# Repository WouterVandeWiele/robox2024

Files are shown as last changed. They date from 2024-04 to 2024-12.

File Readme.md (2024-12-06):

# Robox 2024 (Update is here!)



### status updates
- update 21/10/2024 ==> you can download the update here: https://woutervandewiele.github.io/robox2024/
- update 17/09/2024 ==> We had some issues while testing the update, but we are slowly ironing out most of these issues. The update will contain: possibility of adding radio stations
- update 27/08/2024 ==> We are working on the update.

### planned software updates
- adjusting motor speed in the settings menu (currently being tested)
- fixing full battery indication (currently being tested/in development))
- remembering last played radio station (in development)
- adding a sleep timer (maybe ==> in consideration)

### 1_1_0 update, shoutout to Wouter! (read the dutch part of the manual for the update procedure)
- adding radio stations (read the dutch manual about the part of adding radio stations)
- remembering what audio source was used last, the radio now remembers if you last time played a radio station or a bluetooth stream or ...

### planned mechanical updates
- 3D-printable or foldable glasses (in front of the speakers) ==> in development (30/10/2024)
- Replacing wheels with other fun gadgets (e.g. waving hands) ==> in development (30/10/2024)
- Added a longer version of the ear axle holder, so the wheels are separated a bit further from the body. (see 3D-print files)


- Added a full 3D-printed wheel (as one part)



English version below.

Welkom bij het Robox 2024 (v2) project. Hier vind je alle informatie omtrent dit project. Voor de aanloop van FRI3D hebben we al wat basisinformatie gepubliceerd om je wegwijs te maken met de radio. In de weken na het kamp gaan we nog wat updates toevoegen om de functionaliteit van Robox v2 te verbeteren en uit te breiden. Dus hou deze website in het oog. Er zal dan uitgelegd worden hoe je zelf de udpate kan uitvoeren. Om deze website terug te vinden volstaat het om de QR-code op de achterkant van de radio te scannen.

- status update: de eerste update is klaar en verkrijgbaar. We gaan ook de documentatie op deze site uitbreiden en trachten in het nederlands en engels aan te bieden.
- Voor degenen die het project nog verder willen steunen of een bijdrage willen leveren mogen een donatie doen via https://buymeacoffee.com/erowin
- Heb je vragen over het project kan je via github een issue openen of ons contacteren via discord in deze server: https://discord.gg/HG2vBjpU9c (vragen naar @erowin of @wally)

Welcome at the Robox 2024 (v2) project, here you will find all information about this project. Before FRI3D we have already published some basic information to get to know your radio. In the next comming weeks after the camp we will add some firmware updates to increase the functionality of Robox V2. So keep an eye on this site. There will appear an explanation on how to execute the update all by yourself. To find back this webpage you can scan the QR-code on the back of the radio.

- update: the first firmware update has been releas and can be downloaded here: https://woutervandewiele.github.io/robox2024/ (check the dutch manual for the installation of the update)
- For the ones who want to support the project can donate here: https://buymeacoffee.com/erowin
- If you have questions about the project you can contact us on discord in this server: https://discord.gg/HG2vBjpU9c (you can ask for @erowin or @wally)

## Handleiding

### Beschrijving



1)	Aan/Uit-schakelaar: kan je de luidspreker mee aan of uitzetten. Om te laden dient deze aan te staan.
2)	Menubediening (knop): dient om door de menu’s op het scherm te navigeren. (“bron selectie”, “afspelen”, “instellingen”)
3)	Muziekbediening (knop): dient om de muziek te kunnen bedienen.



Functies:
 
De luidspreker kan muziek afspelen via:

•	Bluetooth

•	Wifi (webradio) 

•	microSD-kaart (.mp3)

•	geen muziekbron

1.	Party modes:

•	Leds op het ritme van de muziek.

•	Wielen die bewegen op het ritme van de muziek.

•	Combinatie van beide.

2.	Batterij:

•	Bijna leeg ==> batterij icoon gaat aan

•	Leeg ==> batterij icoon knippert

•	Opladen wordt aangeduid door een knipperend “zonnetjes” symbool. Als de batterij volgeladen is, dan brandt het “zonnetjes” symbool gewoon.

3.	Menu-items (te bedienen met de menu-knop)
   


### Audiobronnen

Van audiobron wisselen doe je door naar het menu “Bron selectie” te gaan (symbool “dubbele gekruiste pijl). Volgende bronnen zijn beschikbaar:

•	Internetradio ==> Hierbij kan je kiezen tussen verschillende internetradiostations. 

  o	Als je “internetradio” kiest dan zal deze eerst proberen te verbinden met al gekende netwerken. Als deze niets vindt, of het lukt niet, dan zet deze zijn eigen wifi-netwerk op genaamd: “ROBOX-XXXXXXX”. (Zolang de “wifi” niet ingesteld is blijft deze op het scherm vasthangen). Je kan met je gsm/laptop verbinden met het wifi-netwerk van ROBOX, hier kan je dan het gewenste wifi-netwerk toevoegen waarmee ROBOX verbinding moet maken. Normaalgezien opent de webbrowser vervolgens automatisch een website (zie afbeelding rechts). Indien dit niet het geval is, dan kan je het volgende manueel in de adresbalk ingeven: http://192.168.4.1 Op deze website kan je dan het wifi-netwerk kiezen en vervolgens opslaan “save”. ROBOX zal proberen te verbinden met dit netwerk. Als dit niet lukt, dan zet deze terug zijn eigen wifi aan zodat je het opnieuw kan ingeven.



  o	Je kan zelf radiostations toevoegen door naar “Geen bron” te gaan en dan bij “Instellingen” kan je “Webconfiguratie” kiezen. Dan moet je terug surfen met je laptop naar ip adres dat bij in de instellingen staat. Bijvoorbeeld: http://192.168.1.183 in de adresbalk van je webbrowser ingeven.

  

  o	Je krijgt dan deze webpagina te zien waar je een webradiostream kan toevoegen.
  
  

  o	De stream die je toevoegd moet http:// zijn (https:// werkt niet). De link mag ook geen redirect zijn. Je kan dit testen in een webbrowser. Als de link een redirect uitvoert moet je de link hebben na de redirect. Het moet een mp3 stream zijn. Hier kan je de meeste radiostreams (België en wereldwijd) terugvinden: https://fmstream.org/index.php?c=FT

•	Bluetooth ==> Hierbij kan je bluetooth verbinding maken met een gsm/laptop en muziek afspelen. De bluetooth naam vindt je in de “Instellingen”.

•	microSD-kaart (mp3-speler) ==> Hierbij kan je muziek afspelen van een microSD-kaart.

•	Geen bron ==> Dan speelt ROBOX geen muziek af, maar kan je extra instellingen doen via “Instellingen” en “Webconfiguratie” door vervolgens te surfen naar het ip-adres dat ook in “Instellingen” staat. (zie afbeelding rechts)

### Firmware update installeren
- Sluit de radio met een USB-data kabel aan op de pc.
- Ga naar https://woutervandewiele.github.io/robox2024/ en selecteer de meest recente versie, bijvoorbeeld fried_1_1_0.

- Klik vervolgens op install
- Selecteer de juiste com-poort (zie apparaatbeheer ==> poorten om te weten welk apparaat de radio is) en klik op connect.

- Het kan enkele minuten duren vooraleer de update uitgevoerd is.

- Neem contact met ons op als het updaten niet lukt.

## Configuration

main.cpp is configurable through defines to select different examples or components.

### Audio components

Configuration of the arduino audio library components. 
In the context of the robox project they all drive the I2S amp and thus only one can be enabled at a time.

Select one of:

```h
#define ROBOX_FULL          //  the complete audio project, with audio mux

// the examples, from the arduino audio library, with minimal adaptations
#define ROBOX_EXAMPLE_BLE
#define ROBOX_EXAMPLE_SD
#define ROBOX_EXAMPLE_WEB

// robox components, based on the examples above, with adaptations for the audio mux
#define ROBOX_COMPONENT_BLE
#define ROBOX_COMPONENT_WEB
#define ROBOX_COMPONENT_SD
```

### addon components

Additional functionality can be included or removed, multiple can be selected:
```h
#define ROBOX_LCD         // include the LCD component (headers, init and loop)
#define ROBOX_DEBUG_CLI   // include the debug CLI component (headers, init and loop)
```

### wifi credentials

In order to use the webstream component, wifi credentials need to be added to access the web. Follow the instructions here: [wifi credentials](lib/WIFI_CREDENTIALS/README.md)

## Debug CLI

To ease manual testing a debug CLI is added (configurable through the preprocessor statements)
Open a serial connection and when the the ESP starts, follozing messages are displayed if the CLI is initialized.

```
>>> Starting debug CLI.
>Ping was added to the CLI!
>Help was added to the CLI!
>Print was added to the CLI!
>Source was added to the CLI!
>>> CLI installed, type "help" for all options.
```

Currently following options are implemented:
```
help
# help
ping
Replies with "pong" if the ESP32 is still going through the main loop

help
Print cli help, lists all registered commands

print -text <value> [-n <1>]
Example command demonstrating aruments, takes <text> and prints n times

source -s <value>
Select the audio source, takes 1 arument of: ['ble', 'web', 'sd']

mux -meta_title -volume <value>
(get/set mux settings)
-meta_title: reads the current title of the song
-volume: sets the colume on the stream
```

## patching URLStream
In order to check the user URL stream and display an error if the URL is invalid,
a pach is needed on the aurduino audio tools library:

```shell
cp .\URLStream.patch .pio\libdeps\robox_hw\audio-tools
cd .pio\libdeps\robox_hw\audio-tools
cat .\URLStream.patch | git apply
```

## PlatformIO configuration (dev log)
### Freenove fnk0085
https://community.platformio.org/t/esp32s-configuration-error/38647/2

Copy the freenove_fnk0085.json to the projects boards folder.

`.platformio\platforms\espressif32\boards`

## JTAG debugger (ESP32-WROOM-DA)

https://www.youtube.com/watch?v=ENLhW0MQuu0

----

https://www.reddit.com/r/esp32/comments/pvidlt/rst0x10_rtcwdt_rtc_resetboot0x33_spi_fast_flash/

It's always good to read the datasheet. GPIO12 (aka MTDI) is a strapping pin, and when pulled low at boot sets the internal voltage regulator (VDD_SDIO) to 1.8 V. Most dev boards use 3.3 V flash, so... 

----

https://www.reddit.com/r/esp32/comments/yw1w0a/cant_tell_what_name_will_this_show_with_in/

It will work because it's based on the ESP32 generic. The problem is that the DA module has the RF switch connected to 2 different GPIOs that the Wi-Fi API controls.

Be sure you are not using GPIO2 and GPIO25 when using the DA module.

## ESP32 partition calculator
https://esp32.jgarrettcorbin.com/
https://atctwo.net/projects/esp32-partition-editor/

## burn set_flash_voltage

```shell
pip install cryptography
pip install ecdsa
pip install bitstring
pip install reedsolo
```

PlatformIO Core CLI:
```shell
pio pkg exec -- espefuse.py set_flash_voltage 3.3V --port COM3
```

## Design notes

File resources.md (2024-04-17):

# ESP32 DevkitM-1

Devkit speciffic: https://docs.espressif.com/projects/esp-idf/en/stable/esp32/hw-reference/esp32/user-guide-devkitm-1.html

## ESP32 SPI

API & pins: https://docs.espressif.com/projects/esp-idf/en/release-v3.0/api-reference/peripherals/spi_master.html

FAQ HSPI vs VSPI: https://docs.espressif.com/projects/esp-faq/en/latest/software-framework/peripherals/spi.html

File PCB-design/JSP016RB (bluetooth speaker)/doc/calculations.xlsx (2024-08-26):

Motor controller |  |  |  |  |  | Motor selection |  |  | Locked current
Vsense > Vref ==> output power disabled |  |  |  |  |  | 12GAN20-30 | 150RPM | 3V | 0.23 | A
Vref | 0.4114058355 | V | 0,1V < Vref < 0,5V |  |  |  |  |  | correct?
Rtop | 330000 | Ohm
Rbot | 47000 | Ohm
VCC | 3.3 | V
Rsense | 0.8228116711 | Ohm
Vsense | 0.4114058355 | V | (trip point)
Iloadpk | 0.5 | A
Prsense | 0.2057029178 | W
Iloadpk | 0.5142572944 | A
Vsense | 0.4114058355 | V
Rsense | 0.8 | Ohm
Prsense | 0.2115684519 | W
Boost converter
Vin | 3.6 | V | Dnom | 0.371 |  | Dworst | 0.595 |  | Dbest | 0.244
Dnom | 0.371 |  | Vin | 3.7 | V | Vin | 2.7 | V | Vin | 4.2 | V
f | 3800000 | Hz | n | 0.85 |  | n | 0.75 |  | n | 0.9
L | 1e-06 | H | Vout | 5 | V | Vout | 5 | V | Vout | 5 | V
Iout | 1.5 | A
Ilpk | 2.560474521 | A |  | Output cap
 |  |  |  | Cmin | 9.078947368e-06 | F
Worst case |  |  |  | Iout | 1.5 | A
Vin | 3.6 | V |  | Vout | 5 | V
Dworst | 0.595 |  |  | Vin | 2.7 | V
f | 3800000 | Hz |  | f | 3800000 | Hz
L | 1e-06 | H |  | DV | 0.02 | V
Iout | 1.5 | A | ==> may not go higher then this
Ilpk (worst) | 3.985545809 | A

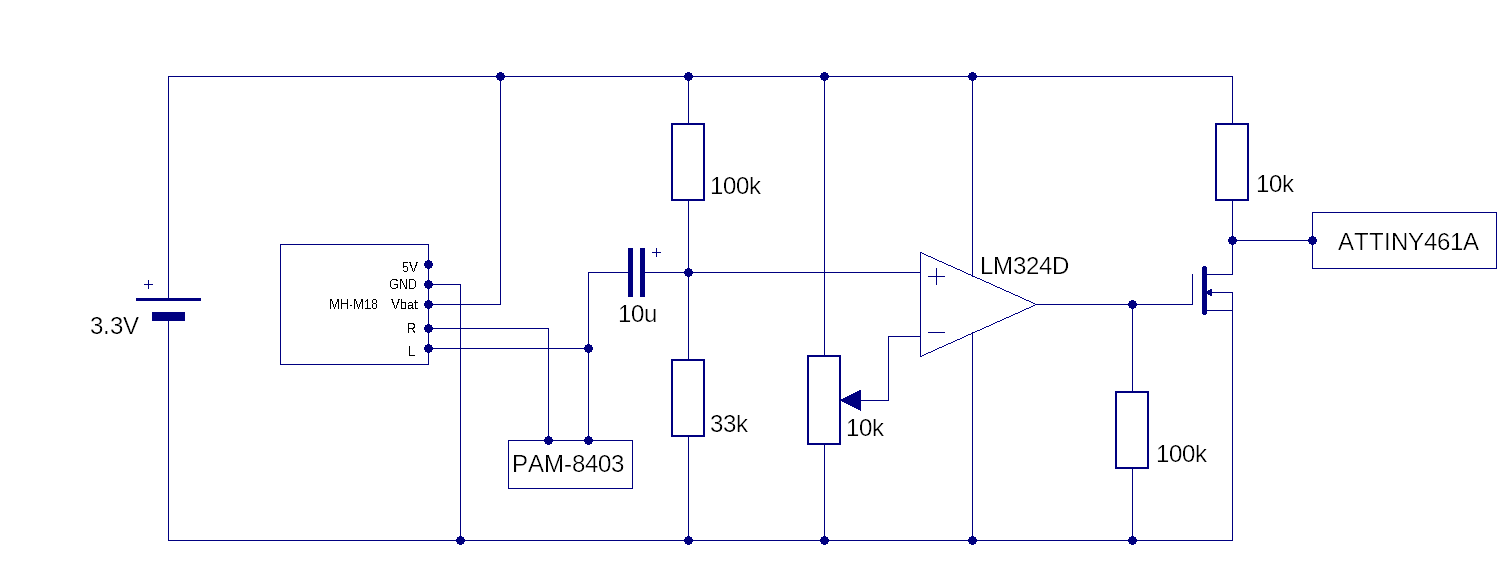
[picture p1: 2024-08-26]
PCB-design/JSP016RB (bluetooth speaker)/robox.BMP

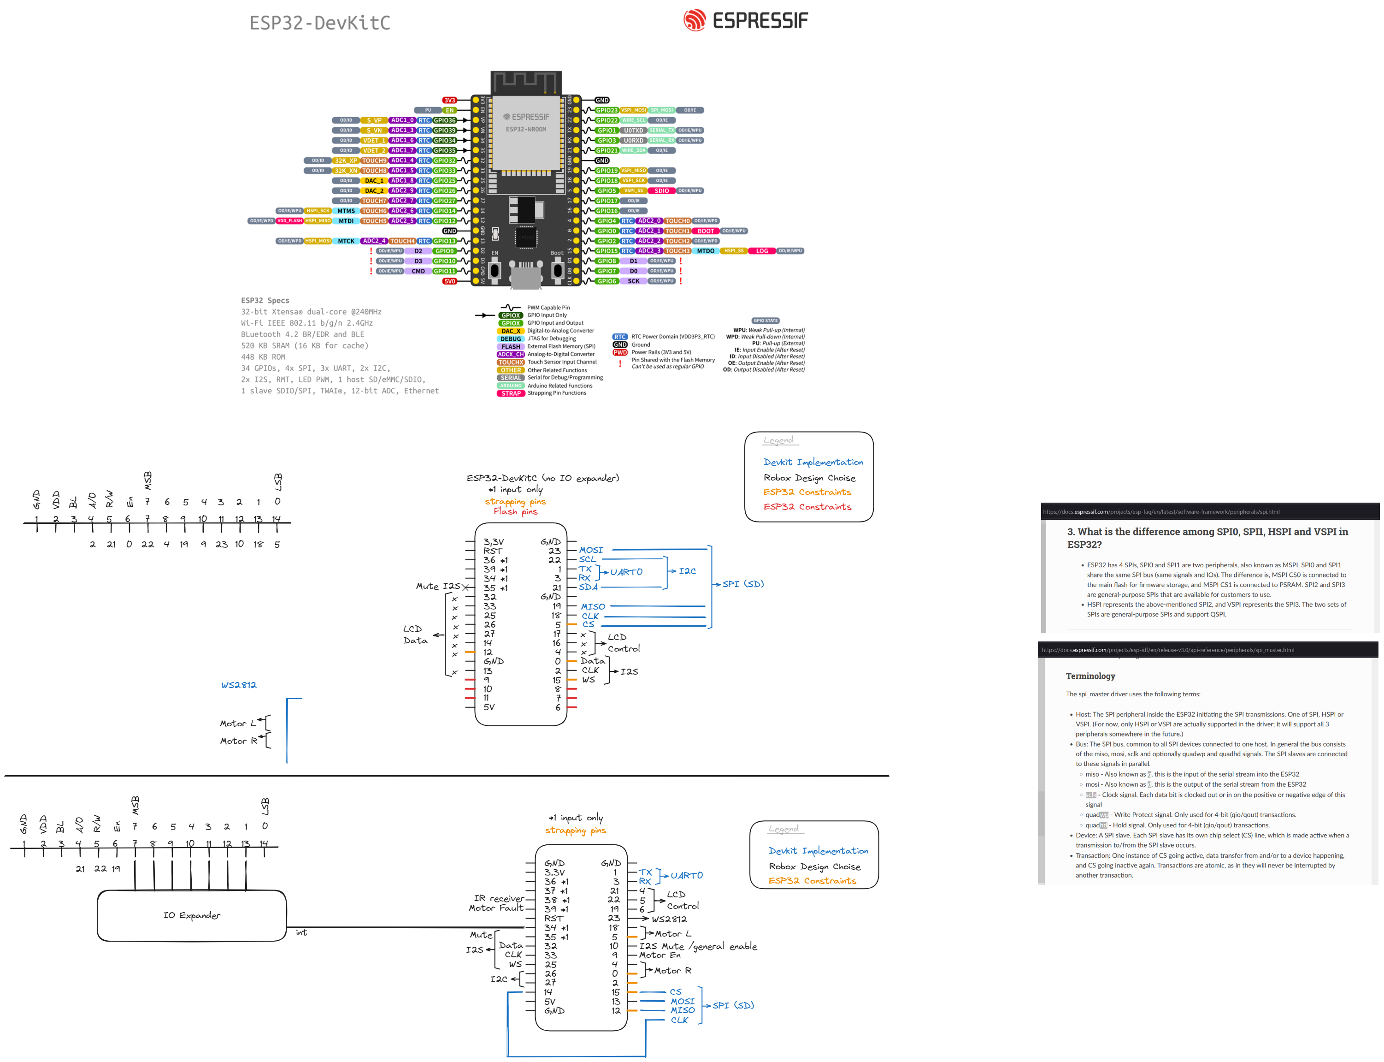
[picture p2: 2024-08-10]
docs/static/pinout_devkitC.excalidraw.png

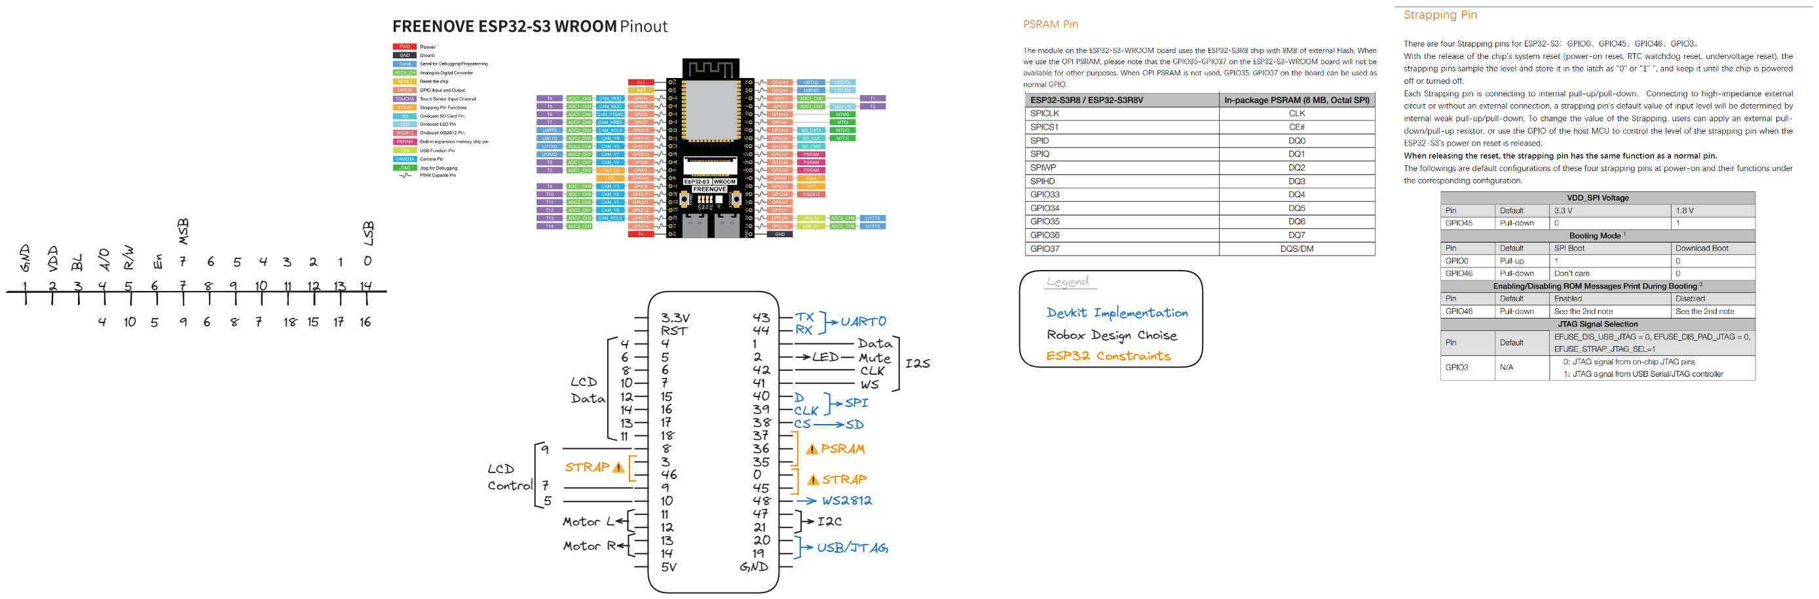
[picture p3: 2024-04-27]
docs/static/pinout_freenove.excalidraw.png

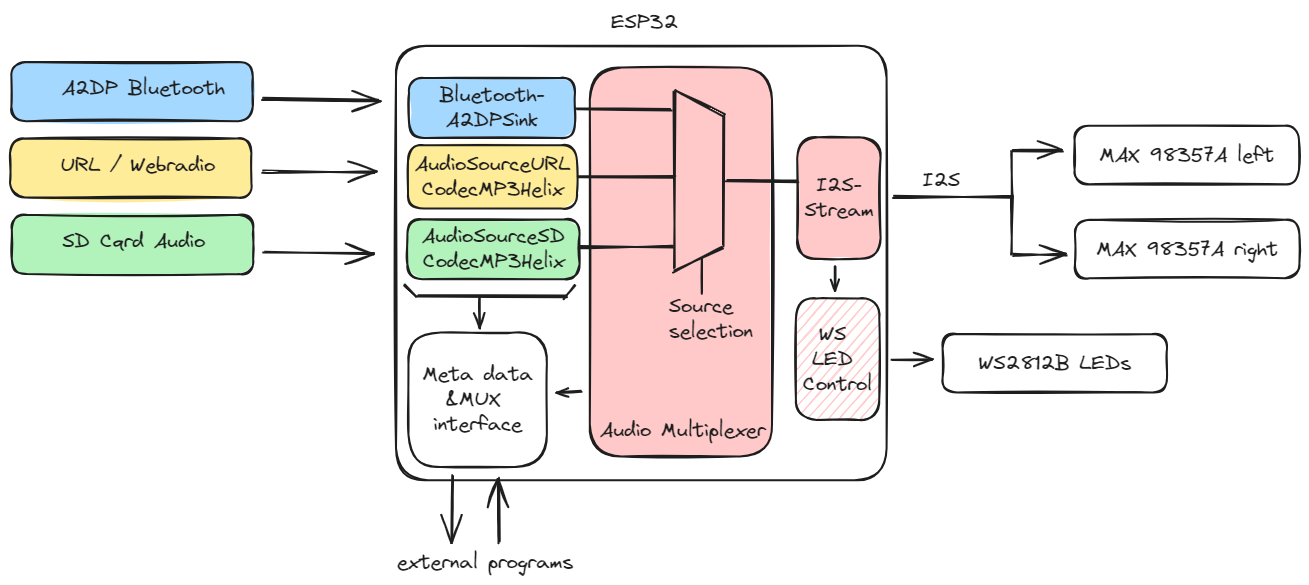
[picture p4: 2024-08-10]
docs/static/audio_overview.excalidraw.png

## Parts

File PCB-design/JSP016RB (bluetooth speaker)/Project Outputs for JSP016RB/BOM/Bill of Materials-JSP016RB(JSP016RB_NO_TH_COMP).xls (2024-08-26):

manufacturer | Description | Designator | LibRef | Quantity | supplier_1 | supplier_1_partnumber
Stackpole Electronics Inc | RES 2.2K OHM 5% 1/16W 0402 | R18 | 52 | 1 | digikey | RMCF0402JT2K20CT-ND
Stackpole Electronics Inc | RES 5.1K OHM 1% 1/16W 0402 | R2, R3 | 94 | 2 | digikey | RMCF0402FT5K10CT-ND
Diodes Incorporated | IC XPNDR 400KHZ I2C 24TSSOP | IC10 | 83 | 1 | digikey | PI4IOE5V6416LEXDICT-ND
Panasonic Electronic Components | RES SMD 330 OHM 1% 1/10W 0402 | R17 | 21 | 1 | digikey | P330LCT-ND
Panasonic Electronic Components | RES SMD 100K OHM 1% 1/10W 0402 | R14, R21, R22, R23, R25, R26, R27, R29, R34, R35, R38, R40, R41, R63, R67, R74, R75 | 7 | 17 | digikey | P100KLCT-ND
Panasonic Electronic Components | RES SMD 10K OHM 1% 1/10W 0402 | R4, R19, R55, R56, R61 | 6 | 5 | digikey | P10.0KLCT-ND
Panasonic Electronic Components | RES SMD 4.7K OHM 1% 1/10W 0402 | R32, R33, R45, R46, R66 | 1 | 5 | digikey | P4.70KLCT-ND
Panasonic Electronic Components | RES SMD 1K OHM 1% 1/10W 0402 | R15, R51 | 0 | 2 | digikey | P1.00KLCT-ND
Panasonic Electronic Components | RES SMD 0 OHM JUMPER 1/10W 0402 | R5, R8, R31, R37, R39, R57, R58, R59, R60, R62, R64, R69, R70, R72, R73 | 8 | 15 | digikey | P0.0JCT-ND
Diodes Incorporated | MOSFET N-CH 100V 170MA SOT23-3 | Q1, Q2, Q5 | 7 | 3 | digikey | NTR4003NT1GOSCT-ND
Maxim Integrated | IC AMP CLASS D MONO 3.2W 16TQFN | IC1, IC2 | 91 | 2 | digikey | MAX98357AETE+TCT-ND
onsemi | MOSFET 2N-CH 6CSP | Q3 | 18 | 1 | digikey | EFC8811R-TFOSCT-ND
Diodes Incorporated | MOSFET P-CH 20V 820MA SOT323 | Q4 | 14 | 1 | digikey | DMG1013UW-7DICT-ND
Stackpole Electronics Inc | RES 0.003 OHM 1% 1.5W 2010 | R20 | 28 | 1 | digikey | CSNL2010FT3L00CT-ND
WCH(Jiangsu Qin Heng) | 2Mbps Transceiver USB 2.0 SOP-16 USB ICs ROHS | IC4 | 79 | 1 | lcsc | C84681
TOPPOWER | IC ESOP-8 Battery Charger Management | IC8 | 89 | 1 | lcsc | C16581
TE Connectivity Passive Product | CRGCQ 0402 27R 1% | R16 | 55 | 1 | digikey | A129608CT-ND
Thin Film Technology Corp. | RES 0.002 OHM 1% 1W 1206 | R52, R53 | 92 | 2 | digikey | 4463-D1MPC1206DR002FF-T5TR-ND
CIT Relay and Switch | SWITCH TOGGLE SPDT 5A 120V | S3 | 3 | 1 | digikey | 2449-ANT11SF1CQE-ND
CUI Devices | MICRO SD CARD CONNECTOR, 8 POSIT | J7 | 56 | 1 | digikey | 2223-MSD-11-ACT-ND
Espressif Systems | RF TXRX MOD BT TRACE ANT CHAS MT | IC3 | 80 | 1 | digikey | 1965-ESP32-MINI-1-N4CT-ND
Nexperia USA Inc. | IC GATE AND 1CH 2-INP 5TSSOP | IC11 | 95 | 1 | digikey | 1727-6053-1-ND
Adafruit Industries LLC | ADDRESS LED DISCRETE RGB 4X2MM | D1, D2 | 86 | 2 | digikey/mouser | 1528-4691-ND/485-4691
Samsung Electro-Mechanics | CAP CER 4.7UF 25V X5R 0805 | C14, C21, C22 | 44 | 3 | digikey | 1276-1244-1-ND
Samsung Electro-Mechanics | CAP CER 1UF 16V X5R 0402 | C16, C18 | 5 | 2 | digikey | 1276-1067-1-ND
Samsung Electro-Mechanics | CAP CER 10000PF 50V X7R 0402 | C48, C49 | 7 | 2 | digikey | 1276-1028-1-ND
Amphenol ICC (Commercial Products) | USB2.0, TYPE C, MID MOUNT, CENTE | J2 | 55 | 1 | digikey | 664-GSB1C4621DS1HRCT-ND
Pulse Electronics | FIXED IND 1UH 5.8A 26 MOHM SMD | L5 | 14 | 1 | digikey | 553-3287-1-ND
Vishay Dale | RES SMD 100 OHM 1% 1/5W 0402 | R6, R28, R43, R44, R47, R48, R65 | 29 | 7 | digikey | 541-100YCT-ND
STMicroelectronics | IC HALF BRIDGE DRV 1.3A 16VFQFPN | IC13 | 81 | 1 | digikey | 497-16604-1-ND
Murata Electronics | CAP CER 10UF 25V X5R 10% SMD | C2, C6, C10, C19, C20, C31, C46 | 1 | 7 | digikey | 490-18214-1-ND
Murata Electronics | CAP CER 0.1UF 50V X5R 0402 | C3, C7, C11, C15, C17, C32, C34, C36, C37, C38, C47 | 0 | 11 | digikey | 490-16356-1-ND
Murata Electronics | THERMISTOR NTC 10KOHM 3380K 0402 | R13 | 1 | 1 | digikey | 490-4801-1-ND
Murata Electronics | CAP CER 0.022UF 50V X7R 0402 | C50 | 53 | 1 | digikey | 490-3884-1-ND
TE Connectivity | SWITCH NAVIGATION DGTL 50MA 12V | S1, S2 | 2 | 2 | digikey | 450-2425755-1CT-ND
TDK Corporation | FERRITE BEAD 120 OHM 0603 1LN | L1, L2, L3, L4 | 4 | 4 | digikey | 445-MMZ1608B121CTAH0CT-ND
YAGEO | CAP CER 1UF 25V X5R 0603 | C12 | 34 | 1 | digikey | 311-1445-1-ND
YAGEO | RES 210K OHM 1% 1/16W 0402 | R1 | 93 | 1 | digikey | 311-210KLRCT-ND
Texas Instruments | 3.8-MHZ, 5.25-V / 4-A BOOST CONV | IC5 | 84 | 1 | digikey | 296-48314-1-ND
Texas Instruments | IC BATT MON LI-ION 1CELL 8X2QFN | IC9 | 94 | 1 | digikey | 296-BQ298012RUGRCT-ND
Diodes Incorporated | IC REG LINEAR 3.3V 600MA SOT89-5 | IC6 | 85 | 1 | digikey | 31-AP2112R5-3.3TRG1CT-ND
YAGEO | RES 330K OHM 1% 1/16W 0402 | R49 | 65 | 1 | digikey | 13-RC0402FR-13330KLCT-ND
Yageo | RES SMD 5K OHM 1% 1/16W 0402 | R10 | 53 | 1 | digikey | 13-RC0402FR-075KLCT-ND
Yageo | RES SMD 46.4K OHM 1% 1/16W 0402 | R7, R24, R30, R36, R42, R50, R54 | 39 | 7 | digikey | 13-AC0402FR-0746K4LCT-ND

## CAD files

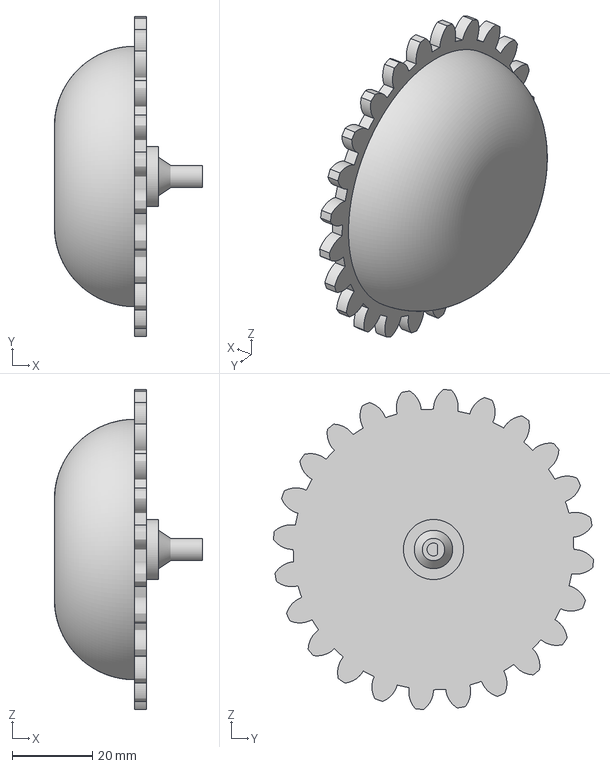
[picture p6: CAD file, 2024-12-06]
Mechanical design/3D-prints/fully-printed-wheel.3mf
37.0 x 79.8 x 79.8 mm

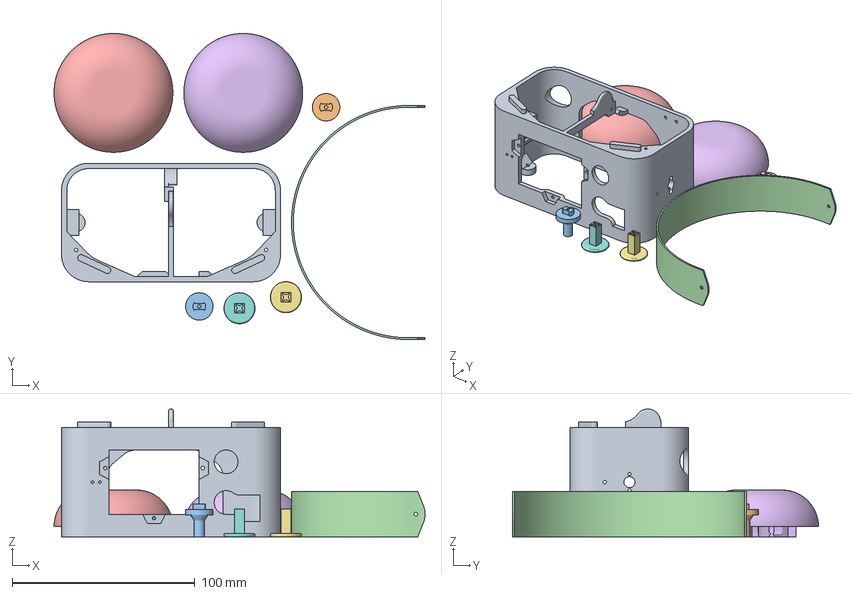
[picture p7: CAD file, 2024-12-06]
Mechanical design/3D-prints/1-full-set.3mf
202.9 x 167.4 x 70.0 mm
frame
ear axle
Headband
ear cap 3
button cap x 2

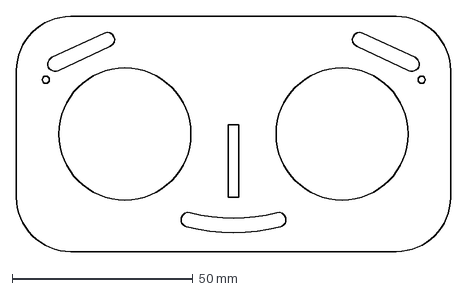
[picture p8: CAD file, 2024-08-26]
Mechanical design/Lasercutting/front plate/front-panel-20240725.dxf
120.0 x 65.0 mm

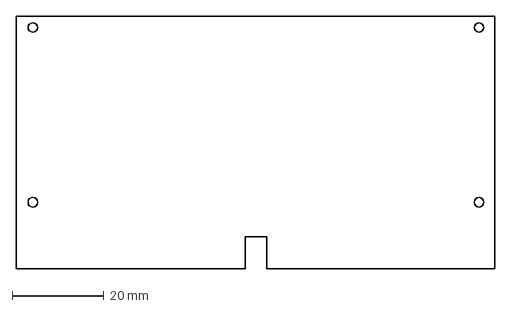
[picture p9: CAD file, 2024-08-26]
PCB-design/JSP016RB (bluetooth speaker)/doc/board-sketch.dxf
104.0 x 55.0 mm

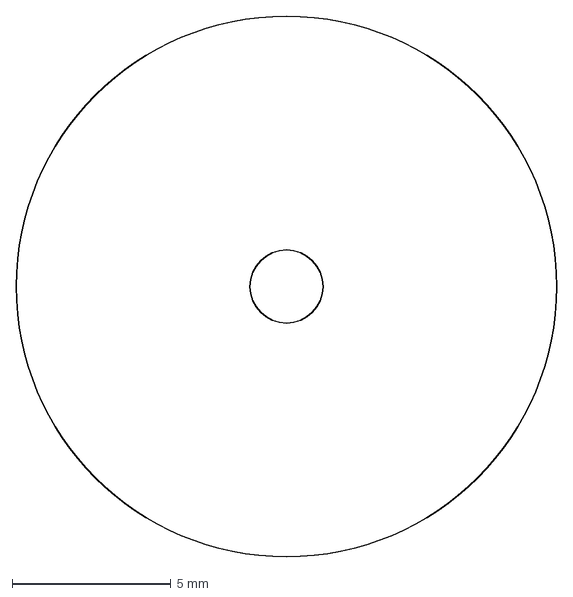
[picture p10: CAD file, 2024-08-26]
Mechanical design/Lasercutting/wheel/ear (gear cap).dxf
17.0 x 17.0 mm

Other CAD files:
Mechanical design/Lasercutting/rear plate/rear panel.dxf
Mechanical design/Lasercutting/sides/side.dxf
Mechanical design/Lasercutting/wheel/wheels.dxf

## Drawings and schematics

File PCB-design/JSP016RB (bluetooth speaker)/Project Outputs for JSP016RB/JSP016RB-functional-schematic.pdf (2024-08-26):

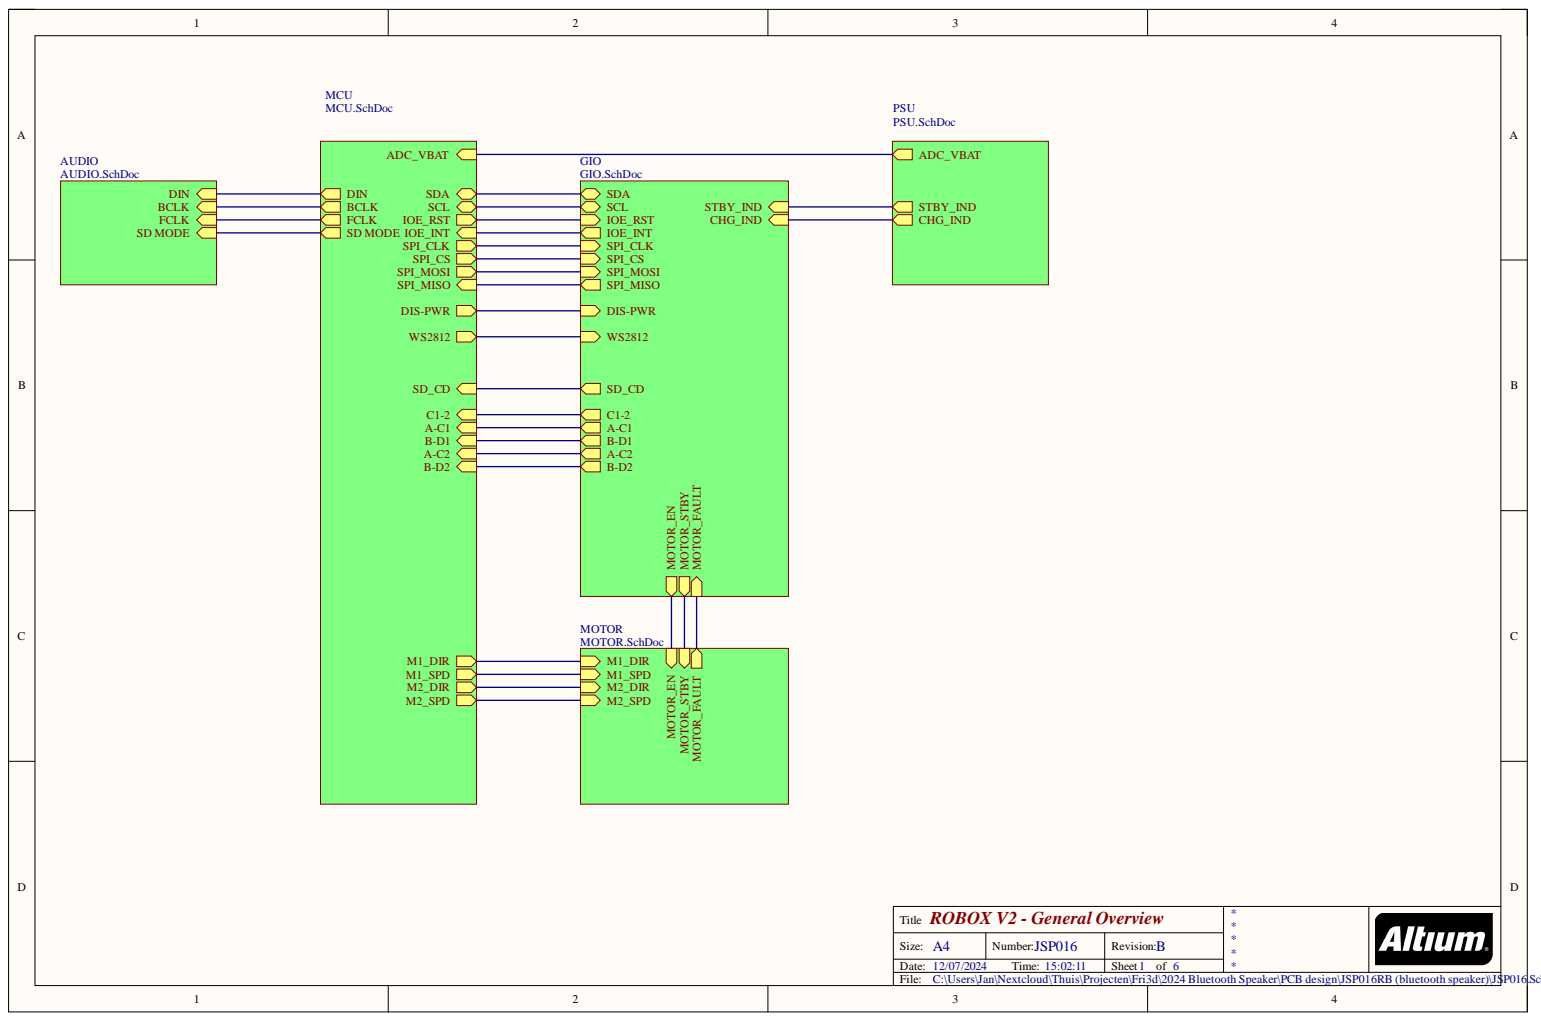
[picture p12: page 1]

C:\Users\Jan\Nextcloud\Thuis\Projecten\Fri3d\2024 Bluetooth Speaker\PCB design\JSP016RB (bluetooth speaker)\JSP016.SchDoc

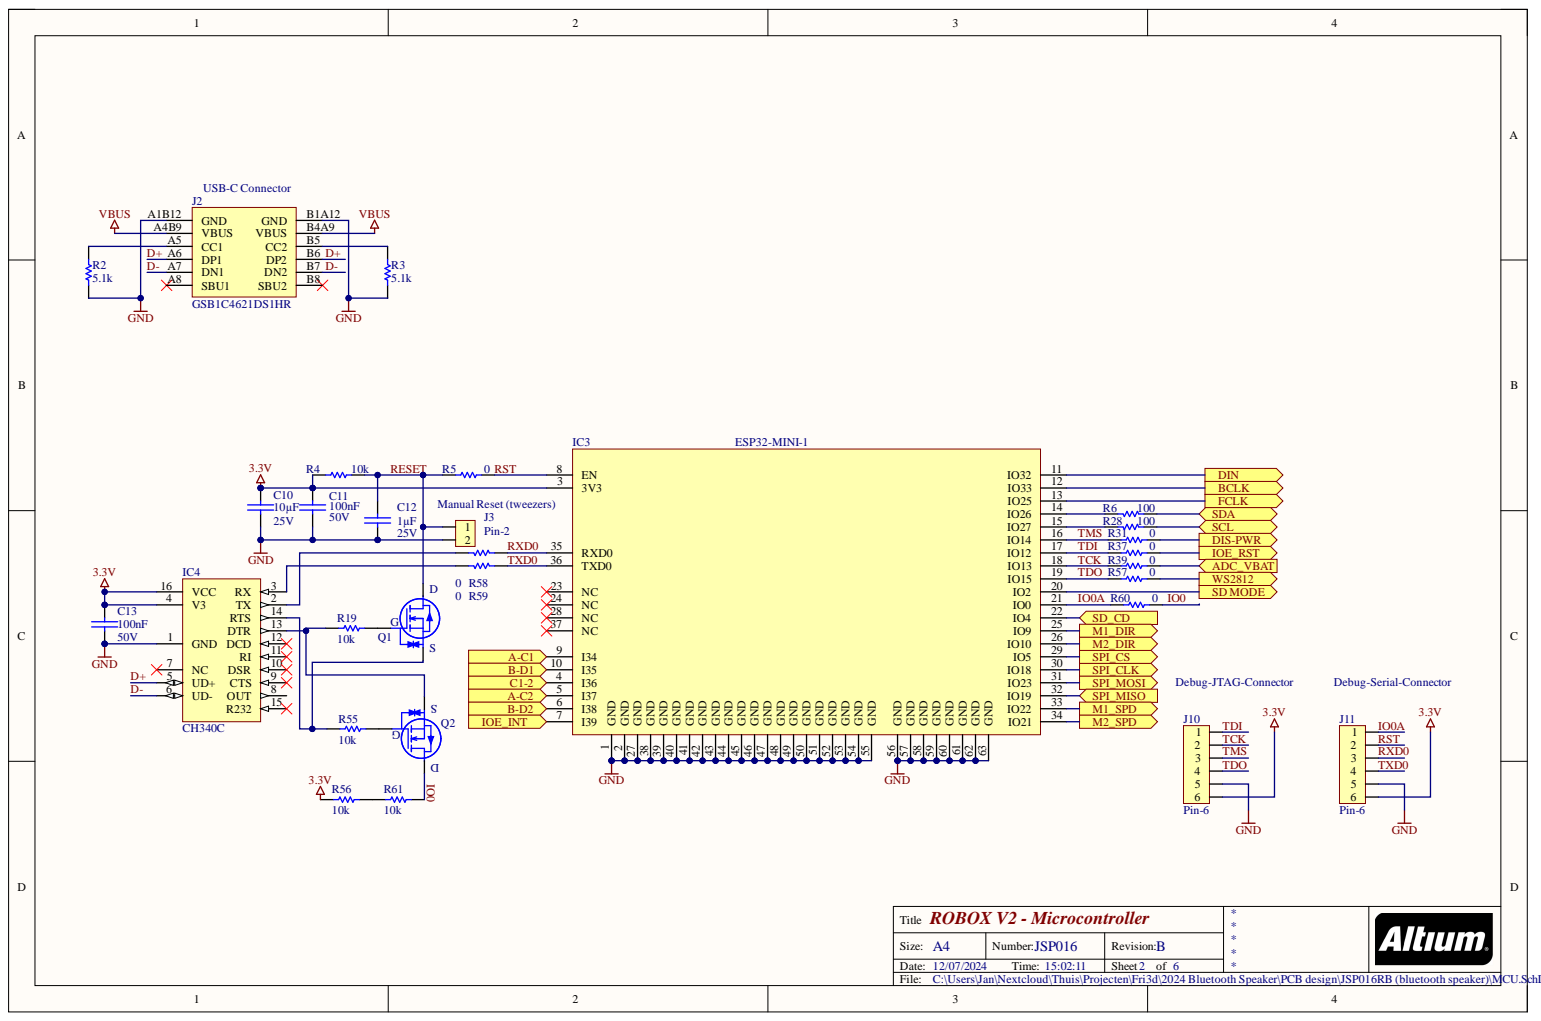
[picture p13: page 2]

C:\Users\Jan\Nextcloud\Thuis\Projecten\Fri3d\2024 Bluetooth Speaker\PCB design\JSP016RB (bluetooth speaker)\MCU.SchDoc

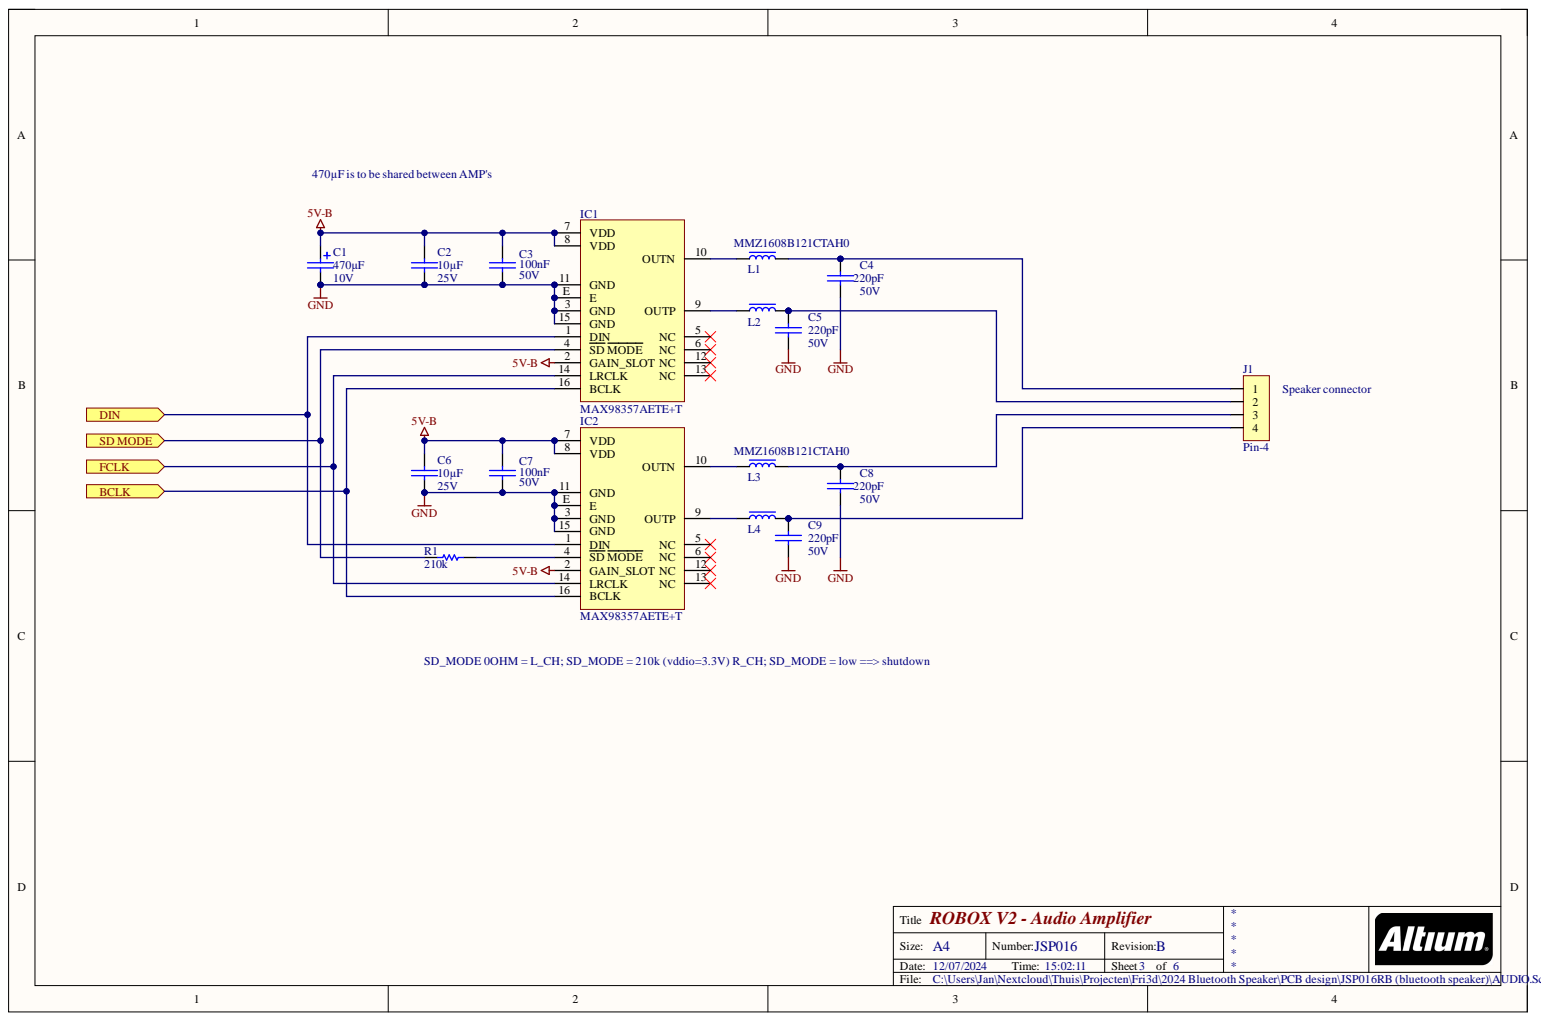
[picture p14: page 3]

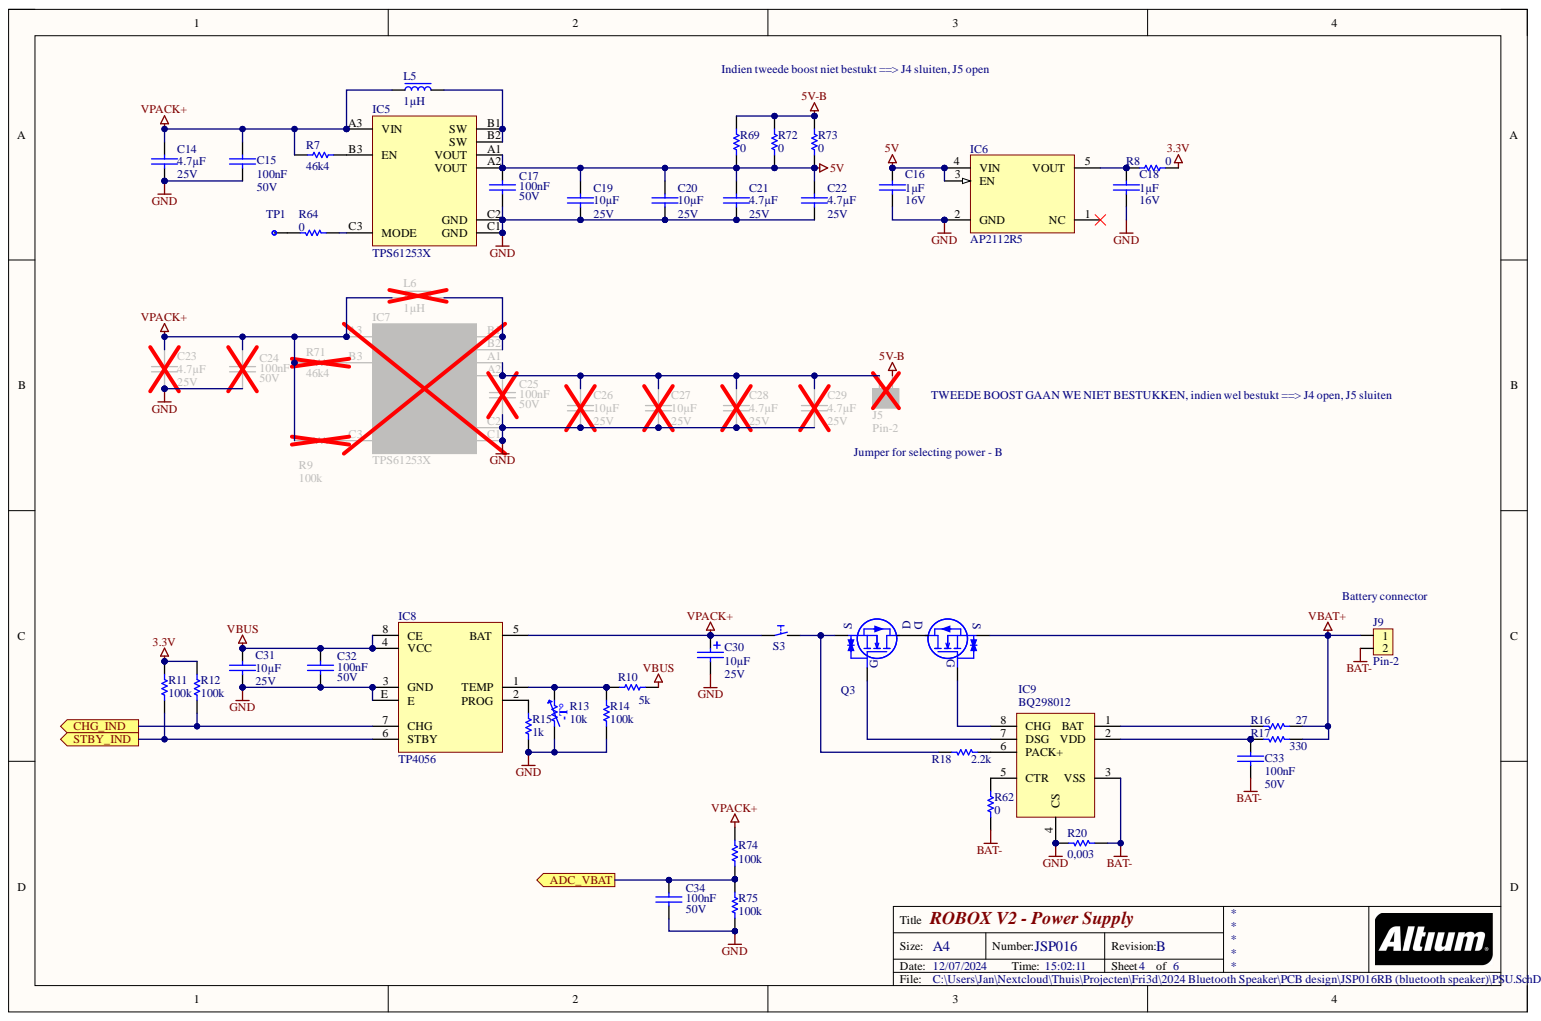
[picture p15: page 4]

Indien tweede boost niet bestukt ==> J4 sluiten, J5 open

TWEEDE BOOST GAAN WE NIET BESTUKKEN, indien wel bestukt ==> J4 open, J5 sluiten

Jumper for selecting power - B

C:\Users\Jan\Nextcloud\Thuis\Projecten\Fri3d\2024 Bluetooth Speaker\PCB design\JSP016RB (bluetooth speaker)\PSU.SchDoc

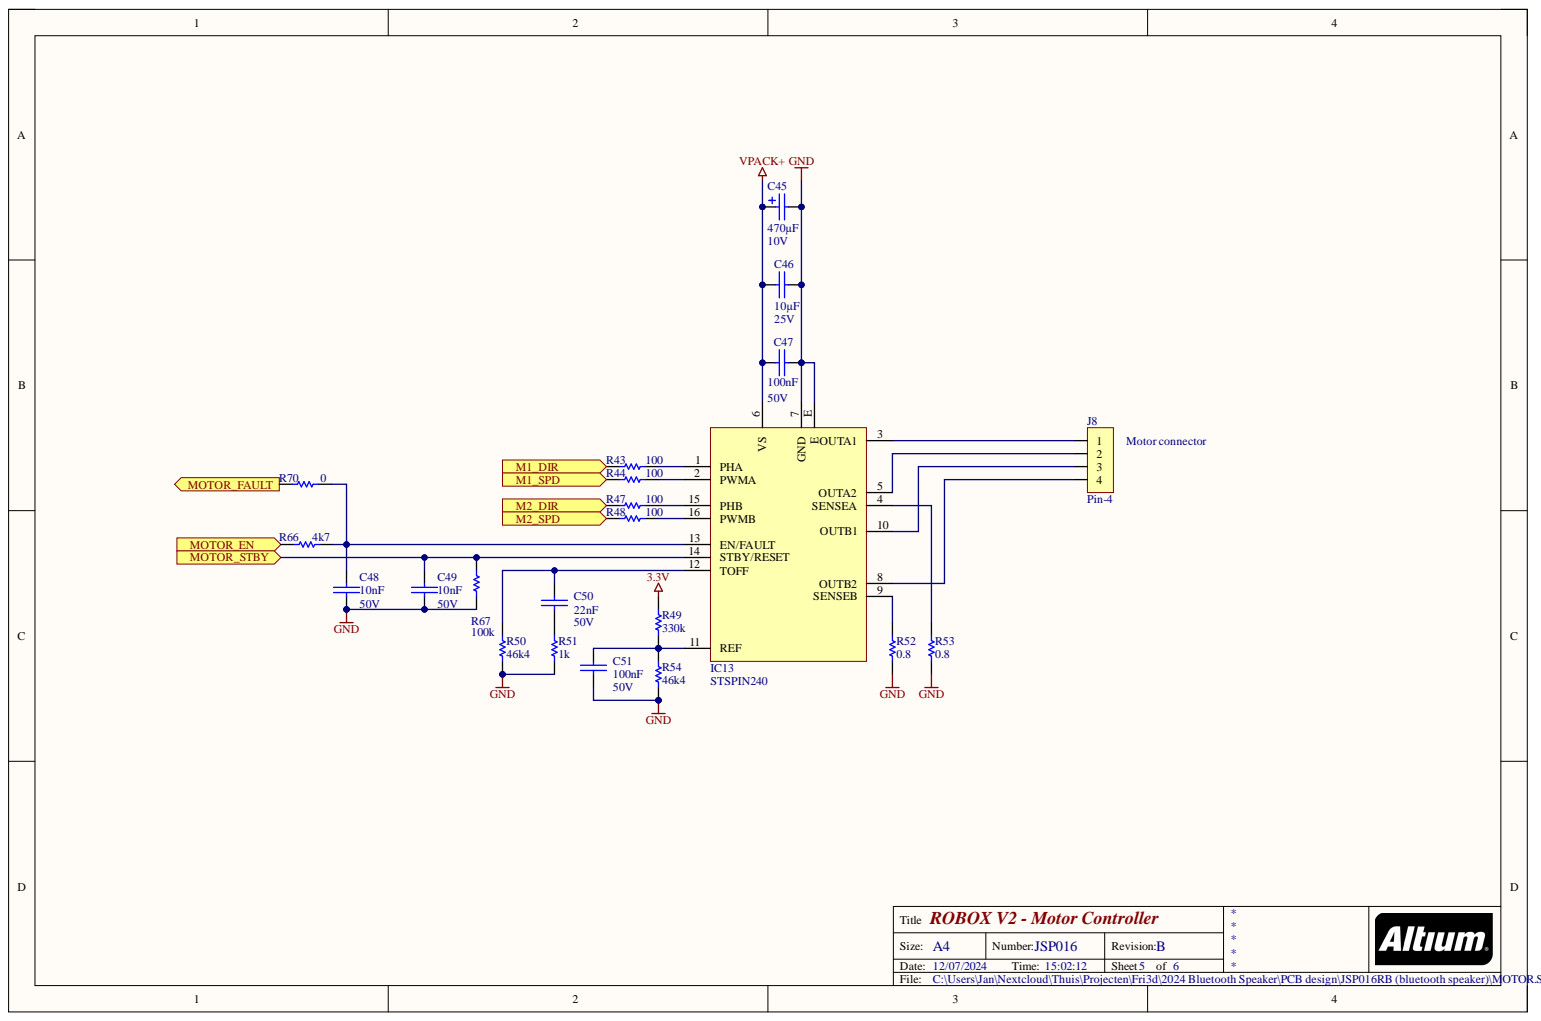
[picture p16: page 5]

C:\Users\Jan\Nextcloud\Thuis\Projecten\Fri3d\2024 Bluetooth Speaker\PCB design\JSP016RB (bluetooth speaker)\MOTOR.SchDoc

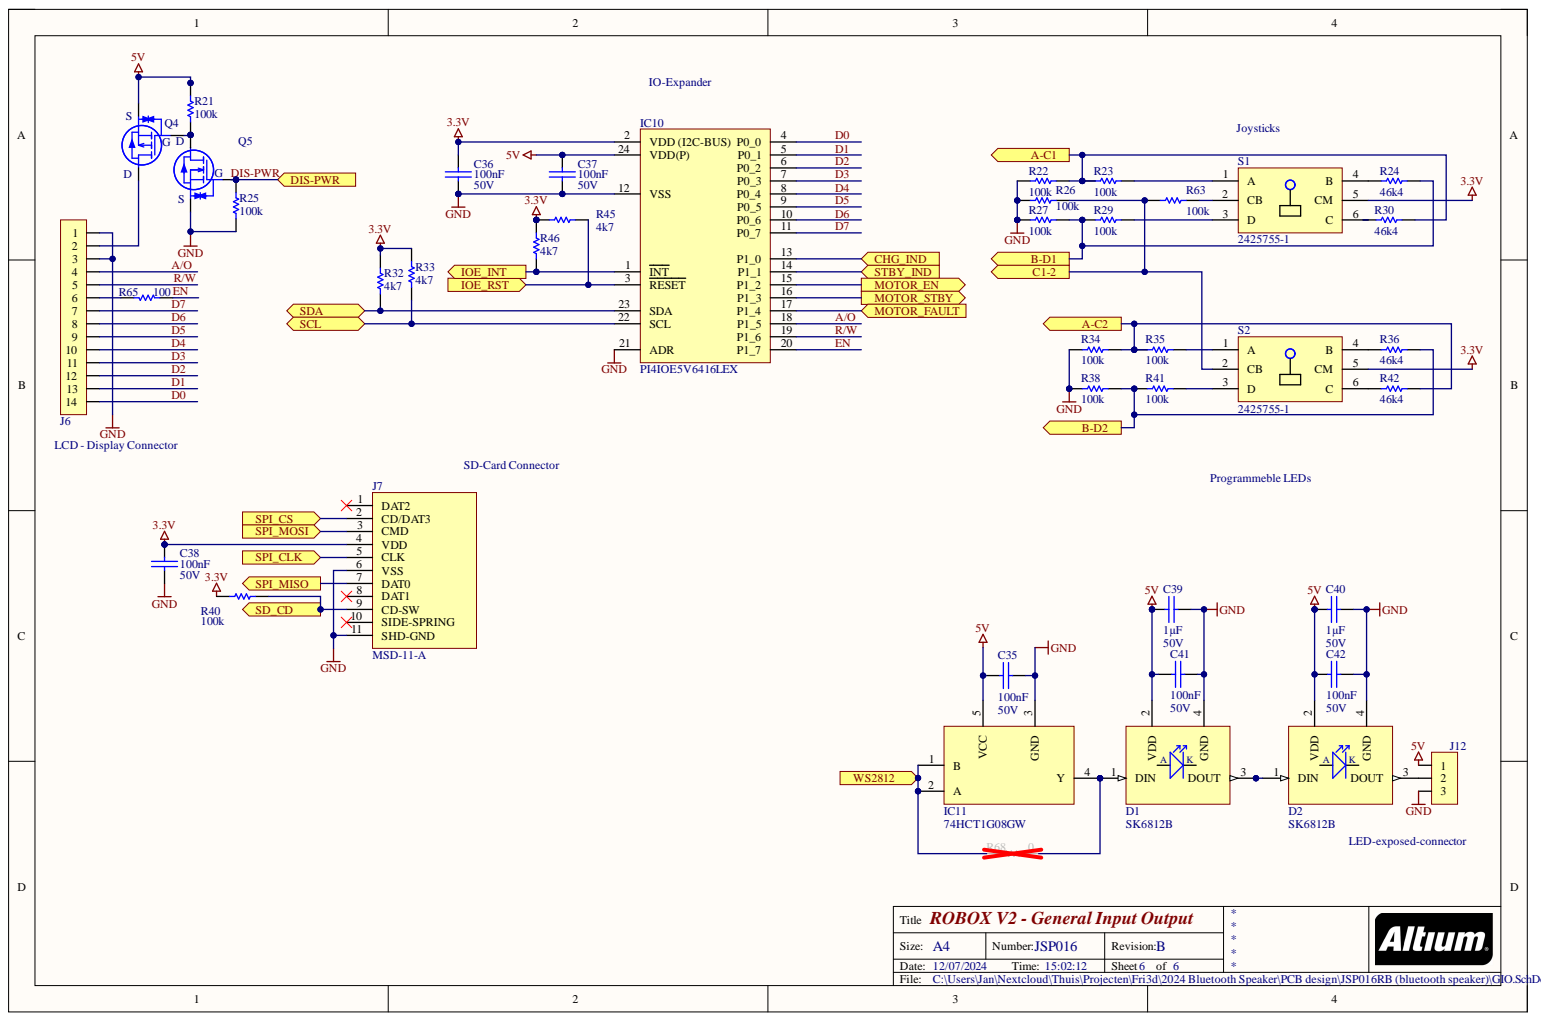
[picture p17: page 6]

DIS-PWR

ROBOX V2 - General Input Output
Title

C:\Users\Jan\Nextcloud\Thuis\Projecten\Fri3d\2024 Bluetooth Speaker\PCB design\JSP016RB (bluetooth speaker)\GIO.SchDoc

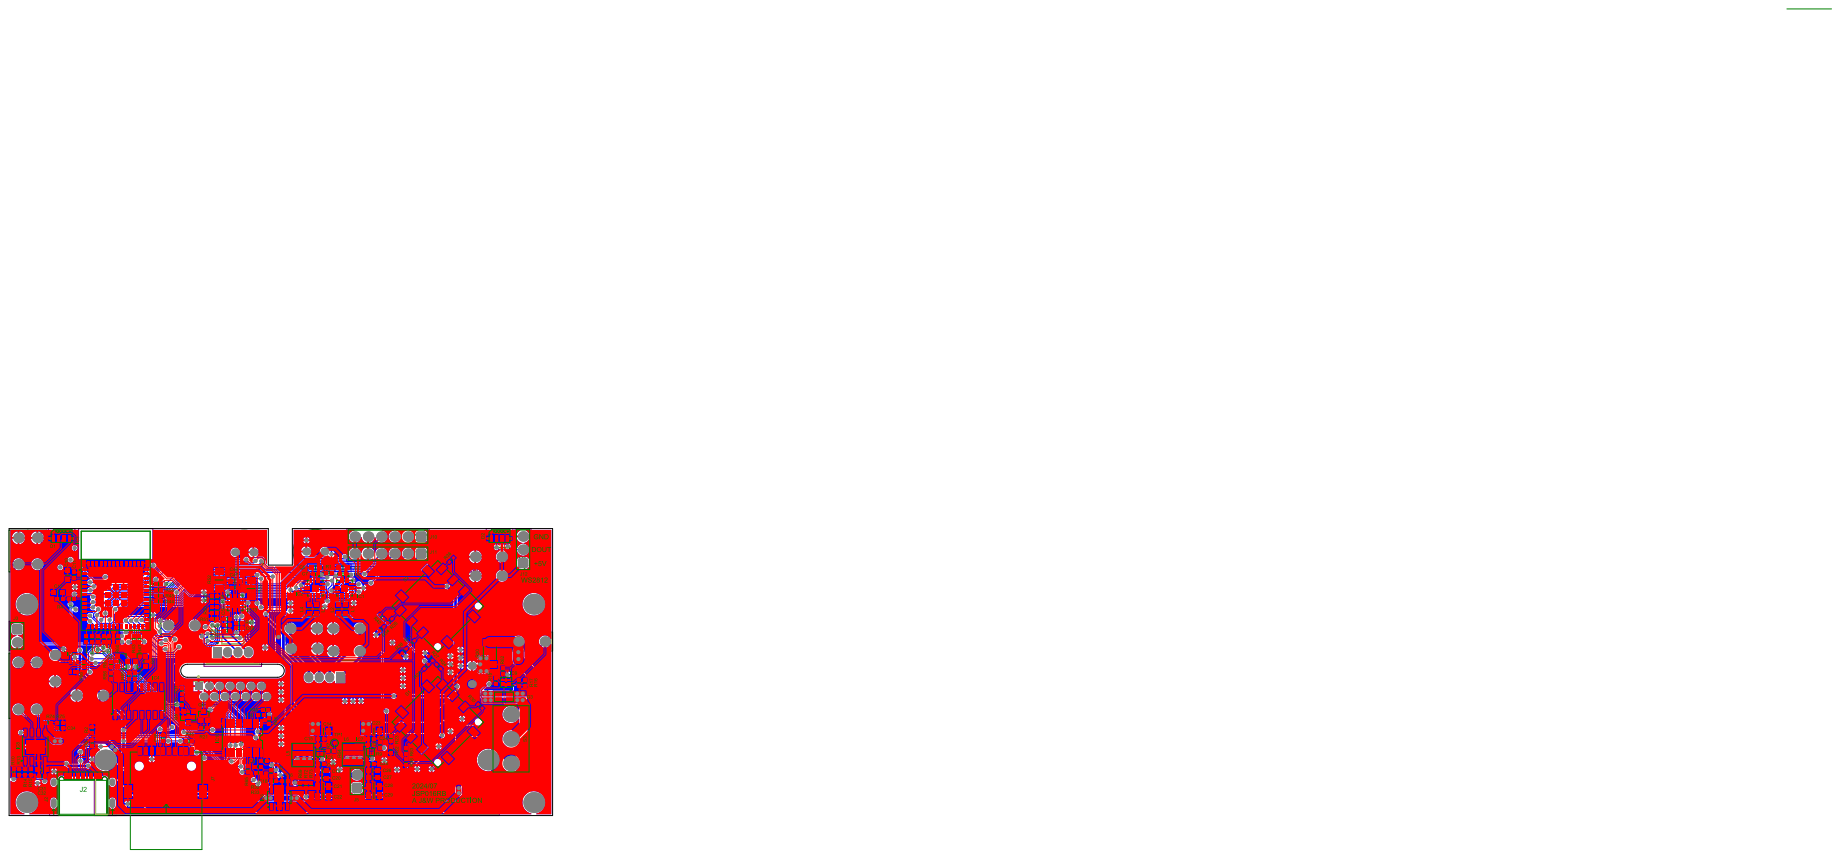
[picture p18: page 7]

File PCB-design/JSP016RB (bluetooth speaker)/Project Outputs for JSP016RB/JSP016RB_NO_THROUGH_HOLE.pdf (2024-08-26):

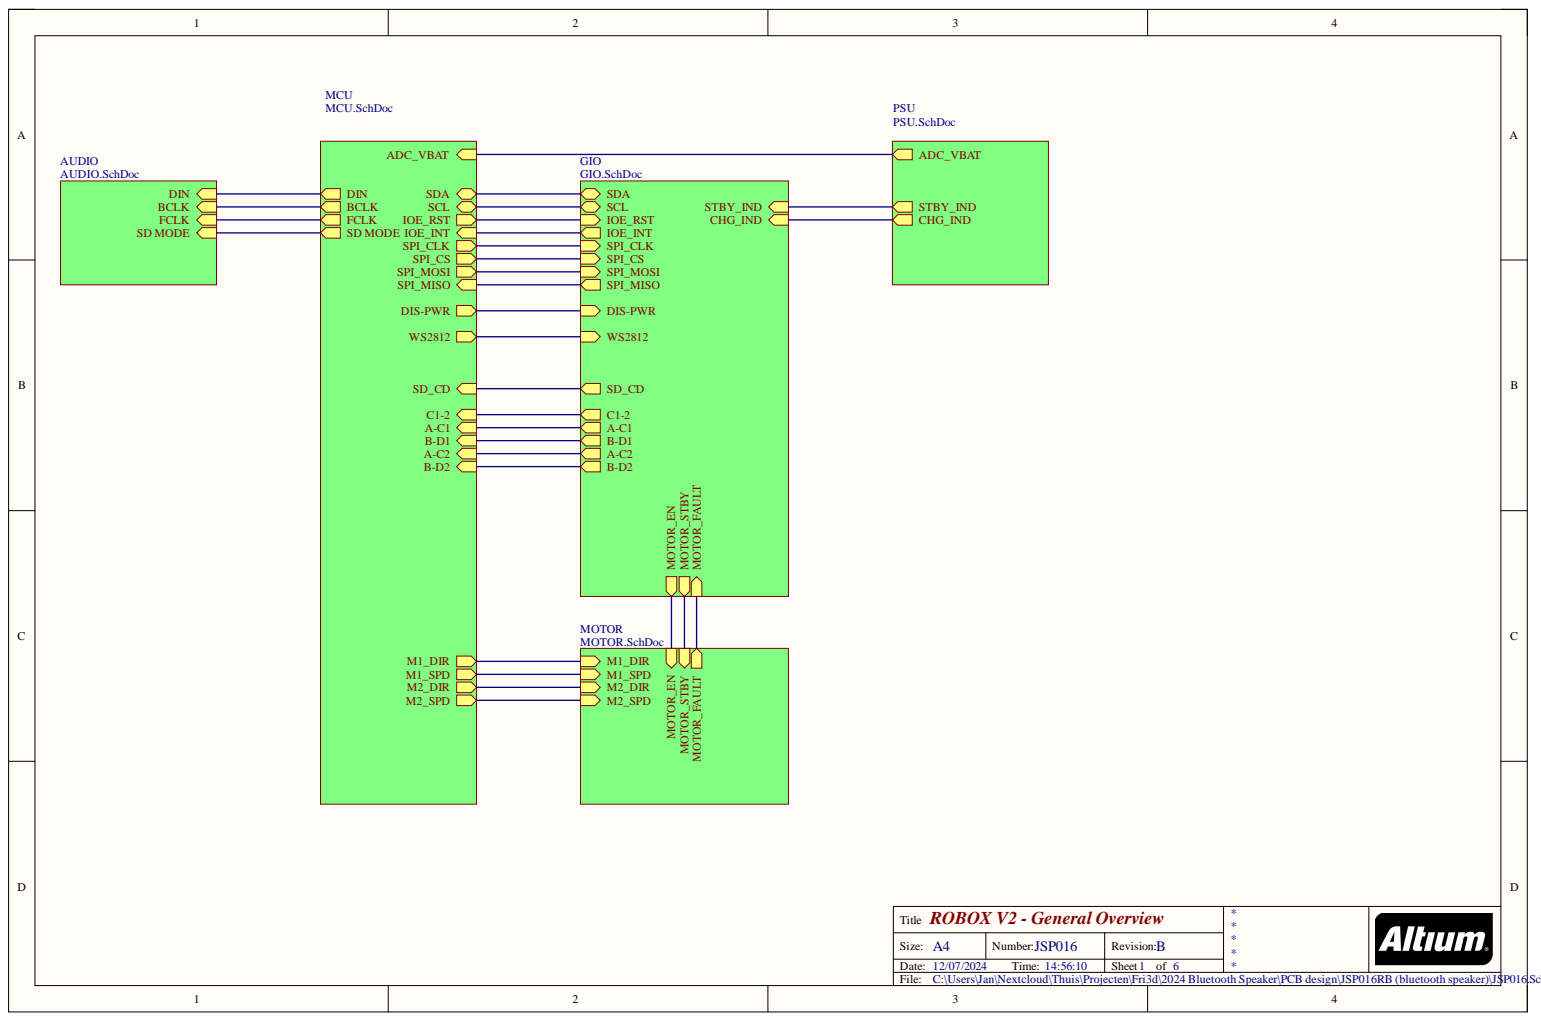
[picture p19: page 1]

C:\Users\Jan\Nextcloud\Thuis\Projecten\Fri3d\2024 Bluetooth Speaker\PCB design\JSP016RB (bluetooth speaker)\JSP016.SchDoc

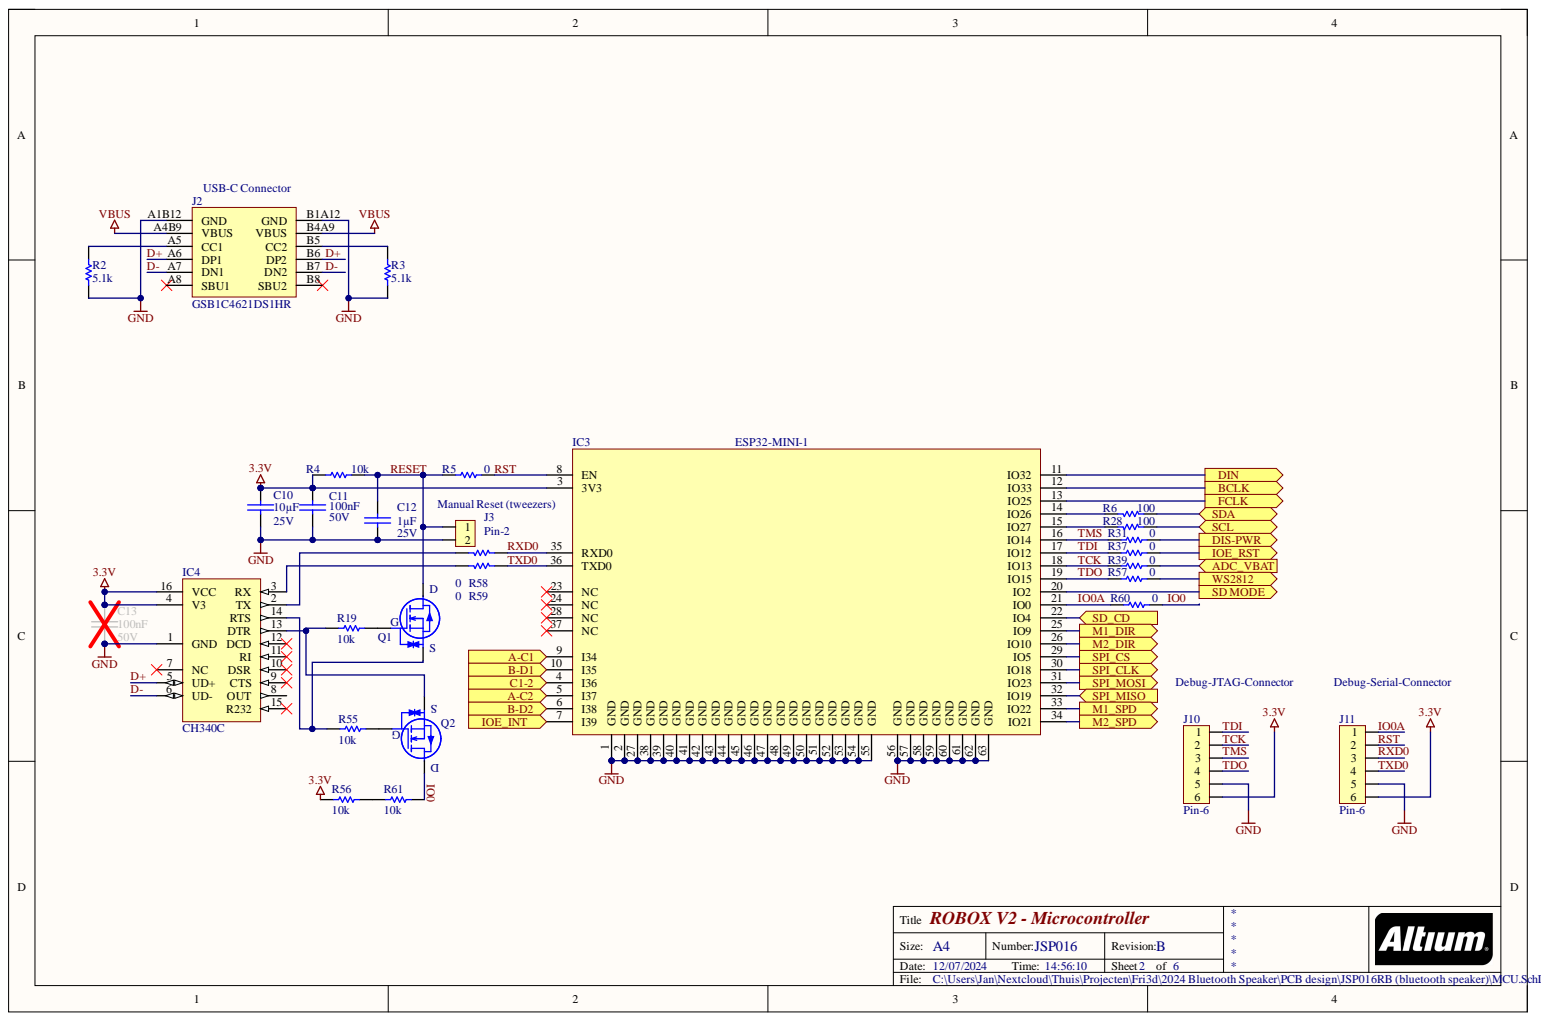
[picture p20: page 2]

C:\Users\Jan\Nextcloud\Thuis\Projecten\Fri3d\2024 Bluetooth Speaker\PCB design\JSP016RB (bluetooth speaker)\MCU.SchDoc

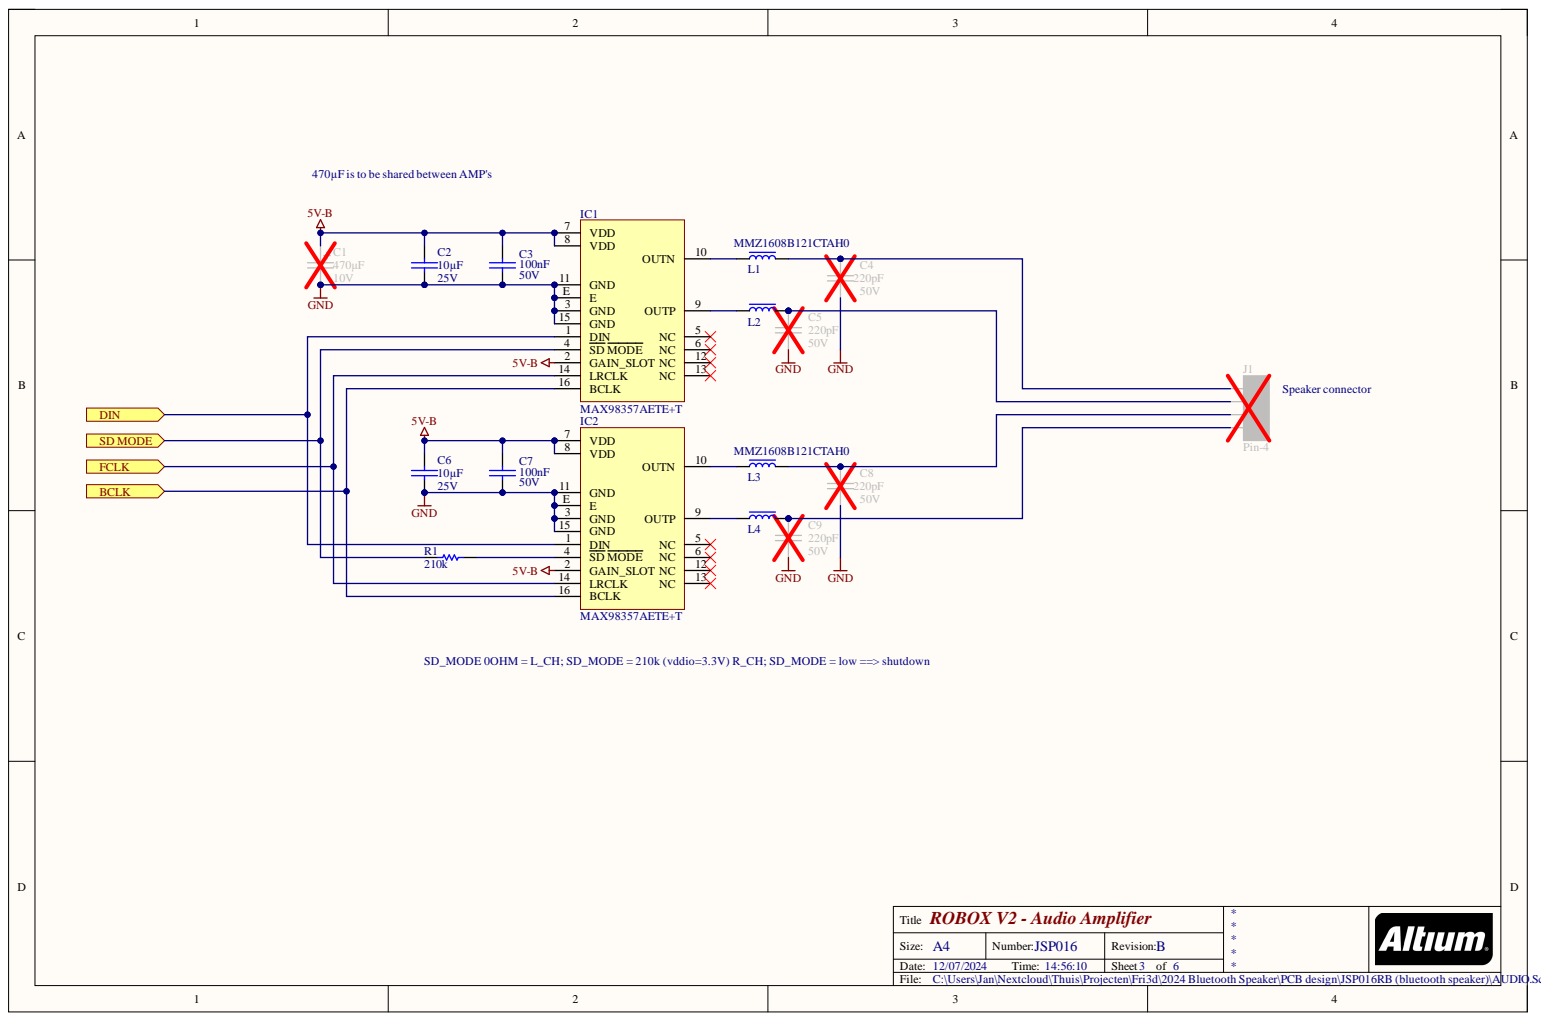
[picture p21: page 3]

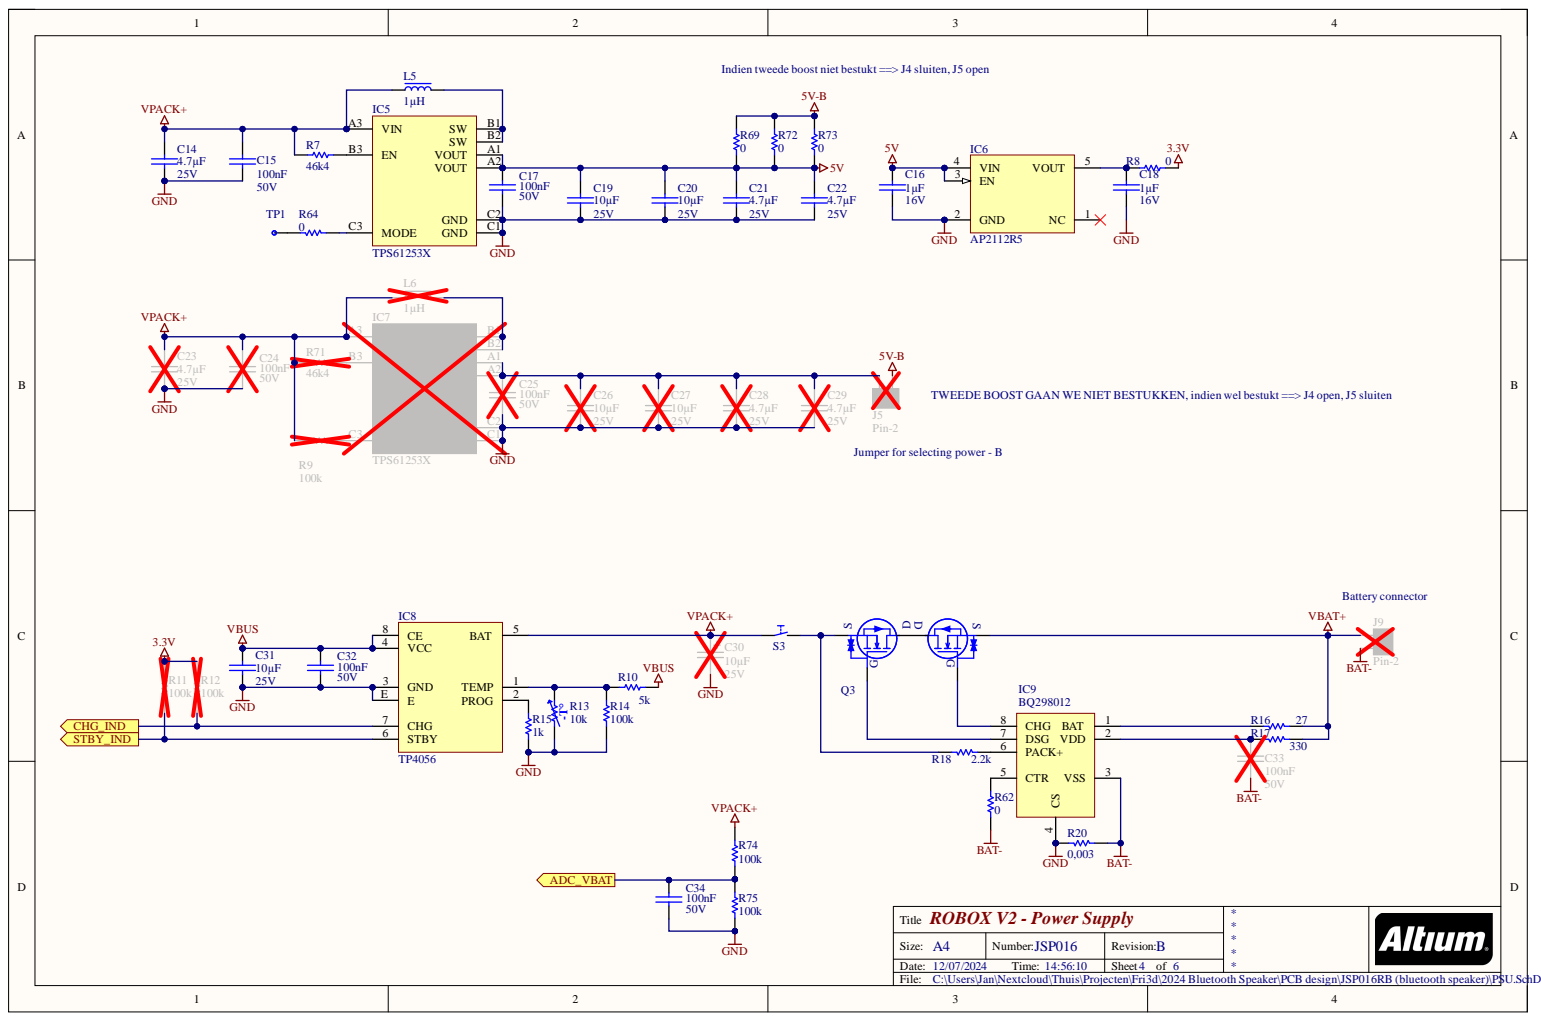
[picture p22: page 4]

Indien tweede boost niet bestukt ==> J4 sluiten, J5 open

TWEEDE BOOST GAAN WE NIET BESTUKKEN, indien wel bestukt ==> J4 open, J5 sluiten

Jumper for selecting power - B

C:\Users\Jan\Nextcloud\Thuis\Projecten\Fri3d\2024 Bluetooth Speaker\PCB design\JSP016RB (bluetooth speaker)\PSU.SchDoc

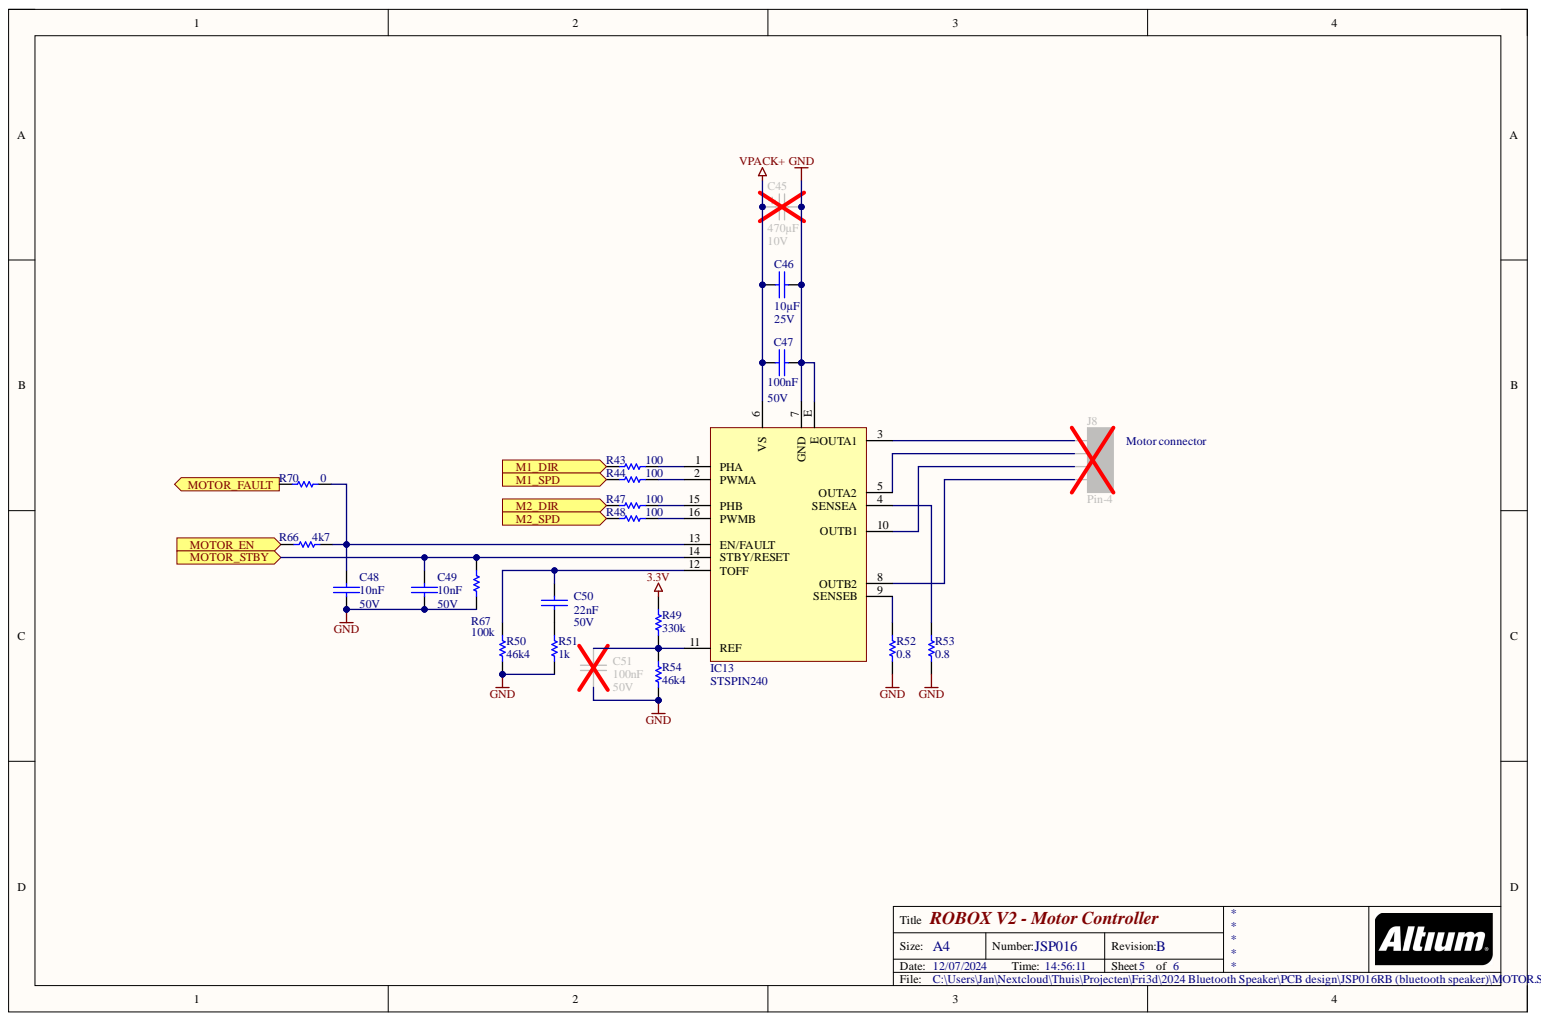
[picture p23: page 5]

C:\Users\Jan\Nextcloud\Thuis\Projecten\Fri3d\2024 Bluetooth Speaker\PCB design\JSP016RB (bluetooth speaker)\MOTOR.SchDoc


DIS-PWR

ROBOX V2 - General Input Output
Title

C:\Users\Jan\Nextcloud\Thuis\Projecten\Fri3d\2024 Bluetooth Speaker\PCB design\JSP016RB (bluetooth speaker)\GIO.SchDoc


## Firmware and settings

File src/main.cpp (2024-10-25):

#include <Arduino.h>
#include "AudioTools.h"

#include "robox_fft_beat.h"

#include "hal/adc_types.h"

/*
 * Compile parts of the project:
 * - ROBOX_FULL: the complete audio project, with audio mux
 * - ROBOX_EXAMPLE_*: the examples, from the arduino audio library, with minimal adaptations
 * - ROBOX_COMPONENT_*: the examples, from the arduino audio library, with adaptations for the audio mux
 *
 * Select only one of the above
 */

#define ROBOX_FULL

// #define ROBOX_EXAMPLE_BLE
// #define ROBOX_EXAMPLE_BLE_BEAT
// #define ROBOX_EXAMPLE_SD
// #define ROBOX_EXAMPLE_SD_PLAYER_BEAT
// #define ROBOX_EXAMPLE_WEB
// #define ROBOX_EXAMPLE_WEB_PLAYER_BEAT
// #define ROBOX_EXAMPLE_MULTI_WEB_FFT

// #define ROBOX_COMPONENT_BLE
// #define ROBOX_COMPONENT_WEB
// #define ROBOX_COMPONENT_SD


/*
 * External parts:
 * ROBOX_LCD: include the LCD component (headers, init and loop)
 * ROBOX_DEBUG_CLI: include the debug CLI component (headers, init and loop)
 * ROBOX_DEBUG_I2C: test the I2C IO expander component
 * ROBOX_DEBUG_I2C_SCANNER: test the I2C, do a scan to detect which HW addresses are active.
 * ROBOX_PREFERENCES: initialize ESP32 NVS as Arduino Preferences
 *
 * Multiple can be selected
 */

#define ROBOX_LCD
#define ROBOX_BATTERY
#define ROBOX_MOTOR
#define ROBOX_TEST_ADC_KEY
// #define ROBOX_DEBUG_CLI
// #define ROBOX_DEBUG_I2C
// #define ROBOX_DEBUG_I2C_SCANNER
#define ROBOX_PREFERENCES
// #define ROBOX_WIFI_MANAGER
// #define ROBOX_WIFI
// #define ROBOX_IMPROV
// #define ROBOX_SERVER
#define ROBOX_RESTART
#define ROBOX_TEST_ADC

// #include "robox_language.h"
// Translator translator(lang_en);

/*
 * compile options logic
 */

#if defined(ROBOX_FULL)
    #include "robox_audio_mux.h"
    extern bool is_ble_connected;
    extern bool is_ble_on;

#elif defined(ROBOX_COMPONENT_BLE)
    #include "robox_ble.h"

#elif defined(ROBOX_COMPONENT_WEB)
    #include "robox_web.h"

#elif defined(ROBOX_COMPONENT_SD)
    #include "robox_sd.h"

#elif defined(ROBOX_EXAMPLE_BLE)
    #include "ble_example.h"

#elif defined(ROBOX_EXAMPLE_BLE_BEAT)
    #include "beat_a2dp_multi.h"

#elif defined(ROBOX_EXAMPLE_SD)
    #include "sdfat_example.h"

#elif defined(ROBOX_EXAMPLE_SD_PLAYER_BEAT)
    #include "beat_sd_player_multi.h"

#elif defined(ROBOX_EXAMPLE_WEB)
    // #include "web_radio.h"
    // #include "web_example_meta2.h"
    #include "player_metadata.h"

#elif defined(ROBOX_EXAMPLE_WEB_PLAYER_BEAT)
    #include "beat_web_player_multi.h"

#elif defined(ROBOX_EXAMPLE_MULTI_WEB_FFT)
    #include "simple_fft_example2.h"

#endif

#if defined(ROBOX_LCD)
    // #include "lcd_config.h"
    #include "lcd_screen.h"
#endif

#if defined(ROBOX_MOTOR)
    #include "robox_motor.h"
#endif

#if defined(ROBOX_TEST_ADC_KEY)
    #include "adc_key.h"
#endif

#if defined(ROBOX_BATTERY)
    #include "robox_battery.h"
#endif

#if defined(ROBOX_DEBUG_CLI)
    #include "debug_cli.h"
#endif

#if defined(ROBOX_DEBUG_I2C)
    #include "robox_io.h"
#endif

#if defined(ROBOX_DEBUG_I2C_SCANNER)
    #include "robox_i2c_scanner.h"
#endif

// #if defined(ROBOX_PREFERENCES)
//     // #include <Preferences.h>
// #endif

#if defined(ROBOX_WIFI_MANAGER)
    #include <WiFiManager.h>          //https://github.com/tzapu/WiFiManager WiFi Configuration Magic
    #include <ESPmDNS.h>
    #include "esp_mac.h"
    // #include <WiFi.h>

    // //needed for library
    // #include <ESPAsyncWebServer.h>
    // #include <ESPAsyncWiFiManager.h>         //https://github.com/tzapu/WiFiManager
#endif

#if defined(ROBOX_WIFI)
    #include "robox_wifi.h"
#endif

#if defined(ROBOX_IMPROV)
    #include <ImprovWiFiLibrary.h>
    ImprovWiFi improvSerial(&Serial);
#endif

// #if defined(ROBOX_SERVER)
//     #include "robox_server.h"
// #endif

#if defined(ROBOX_RESTART)
    #include "robox_restart.h"
    RoboxRestartManager restart_manager;
#endif

#include "robox_led_motor_controller.h"
LedMotorController led_motor_controller;

#if defined(ROBOX_TEST_ADC)
int adc2_pin13;
uint64_t adc_timekeeper = 5000;
extern uint32_t beat_loop_timestamp;
static uint32_t beat_loop_timestamp_previous = 0;
#endif

// #include "ble_example.h"
// #include "ble_copier.h"
// #include "streams_copy_example.h"
// #include "listing.h"
#include "general_definitions.h"
// #include "wifi_credentials.h"

// setup logging
// #define LOG_LOCAL_LEVEL ESP_LOG_ERROR
#include "esp_log.h"
// #include "esp32-hal-log.h"

// #define MP3_MAX_OUTPUT_SIZE 2048*5//1024 * 5
// #define MP3_MAX_FRAME_SIZE 65536 //1600

// #define DEFAULT_BUFFER_SIZE 4096 //1024
// #define I2S_BUFFER_SIZE 1024 //512

// #define PREFER_FIXEDPOINT 

// typedef int16_t sound_t;                                   // sound will be represented as int16_t (with 2 bytes)



#if defined(ROBOX_FULL)
    RoboxAudioMux mux;
    static TaskHandle_t AudioCopyTask;

#elif defined(ROBOX_COMPONENT_BLE)
    RoboxBluetooth ble;

#elif defined(ROBOX_COMPONENT_WEB)
    RoboxWebRadio web;

#elif defined(ROBOX_COMPONENT_SD)
    RoboxSD sd;

#endif

#if defined(ROBOX_DEBUG_I2C) || defined(ROBOX_LCD) || defined(ROBOX_MOTOR) || defined(ROBOX_BATTERY)
static RoboxIoExpander* io;
#endif

#if defined(ROBOX_LCD)
static RoboxLcdScreen* screen;
#endif

#if defined(ROBOX_MOTOR)
RoboxMotor* motor;
unsigned long timekeeper = 0;
uint8_t motor_test_program = 0;
#define MOTOR_TEST_PROGRAMS 4
#endif

#if defined(ROBOX_BATTERY)
RoboxBattery* battery;
#endif


// #if defined(ROBOX_PREFERENCES)
// // Preferences roboxPrefs;
// // const char* wifi_ssid_2;
// // const char* wifi_password_2;
// // bool motorsOn;
// #endif

#if defined(ROBOX_WIFI_MANAGER)
    WiFiManager wifiManager;

    unsigned int  timeout   = 120; // seconds to run for
    unsigned int  startTime = millis();
    bool portalRunning      = false;
    bool startAP            = false; // start AP and webserver if true, else start only webserver

    // static AsyncWebServer server_manager(80);
    // static DNSServer dns;
    // static AsyncWiFiManager wifiManager(&server_manager,&dns);

    void doWiFiManager(){
  // is auto timeout portal running
  if(portalRunning){
    wifiManager.process(); // do processing

    // check for timeout
    if((millis()-startTime) > (timeout*1000)){
      Serial.println("portaltimeout");
      portalRunning = false;
      if(startAP){
        wifiManager.stopConfigPortal();
      }
      else{
        wifiManager.stopWebPortal();
      } 
   }
  }

  // is configuration portal requested?
  if(!portalRunning) {
    if(startAP){
      Serial.println("Button Pressed, Starting Config Portal");
      wifiManager.setConfigPortalBlocking(false);
      wifiManager.startConfigPortal();
    }  
    else{
      Serial.println("Button Pressed, Starting Web Portal");
      wifiManager.startWebPortal();
    }  
    portalRunning = true;
    startTime = millis();
  }
}
#endif


[[noreturn]] void audio_task(void* parameter) {
    mux.setup();

    while (true) {
        mux.copy();
        vTaskDelay(1);
    }
}

void setup() {
    Serial.begin(115200);

    AudioLogger::instance().begin(Serial, AudioLogger::Info);

    restart_manager.init();

    // font generated with https://patorjk.com/software/taag/#p=display&f=Doh&t=ROBOX
    Serial.println("\n");
    Serial.println("RRRRRRRRRRRRRRRRR        OOOOOOOOO     BBBBBBBBBBBBBBBBB        OOOOOOOOO     XXXXXXX       XXXXXXX");
    Serial.println("R::::::::::::::::R     OO:::::::::OO   B::::::::::::::::B     OO:::::::::OO   X:::::X       X:::::X");
    Serial.println("R::::::RRRRRR:::::R  OO:::::::::::::OO B::::::BBBBBB:::::B  OO:::::::::::::OO X:::::X       X:::::X");
    Serial.println("RR:::::R     R:::::RO:::::::OOO:::::::OBB:::::B     B:::::BO:::::::OOO:::::::OX::::::X     X::::::X");
    Serial.println("  R::::R     R:::::RO::::::O   O::::::O  B::::B     B:::::BO::::::O   O::::::OXXX:::::X   X:::::XXX");
    Serial.println("  R::::R     R:::::RO:::::O     O:::::O  B::::B     B:::::BO:::::O     O:::::O   X:::::X X:::::X   ");
    Serial.println("  R::::RRRRRR:::::R O:::::O     O:::::O  B::::BBBBBB:::::B O:::::O     O:::::O    X:::::X:::::X    ");
    Serial.println("  R:::::::::::::RR  O:::::O     O:::::O  B:::::::::::::BB  O:::::O     O:::::O     X:::::::::X     ");
    Serial.println("  R::::RRRRRR:::::R O:::::O     O:::::O  B::::BBBBBB:::::B O:::::O     O:::::O     X:::::::::X     ");
    Serial.println("  R::::R     R:::::RO:::::O     O:::::O  B::::B     B:::::BO:::::O     O:::::O    X:::::X:::::X    ");
    Serial.println("  R::::R     R:::::RO:::::O     O:::::O  B::::B     B:::::BO:::::O     O:::::O   X:::::X X:::::X   ");
    Serial.println("  R::::R     R:::::RO::::::O   O::::::O  B::::B     B:::::BO::::::O   O::::::OXXX:::::X   X:::::XXX");
    Serial.println("RR:::::R     R:::::RO:::::::OOO:::::::OBB:::::BBBBBB::::::BO:::::::OOO:::::::OX::::::X     X::::::X");
    Serial.println("R::::::R     R:::::R OO:::::::::::::OO B:::::::::::::::::B  OO:::::::::::::OO X:::::X       X:::::X");
    Serial.println("R::::::R     R:::::R   OO:::::::::OO   B::::::::::::::::B     OO:::::::::OO   X:::::X       X:::::X");
    Serial.println("RRRRRRRR     RRRRRRR     OOOOOOOOO     BBBBBBBBBBBBBBBBB        OOOOOOOOO     XXXXXXX       XXXXXXX");
    Serial.println("\n");
    Serial.println("Version:");
    Serial.println(ROBOX_VERSION);
    Serial.println("\n");
    Serial.println("More info on https://woutervandewiele.github.io/robox2024/\n");
    Serial.println("\n");

    // setup logging
    esp_log_level_set("*", ESP_LOG_ERROR);
    // esp_log_level_set("*", ESP_LOG_WARN);
    // esp_log_level_set(LOG_MAIN_TAG, ESP_LOG_DEBUG);
    // esp_log_level_set(LOG_BLE_TAG, ESP_LOG_DEBUG);
    // esp_log_level_set(LOG_MUX_TAG, ESP_LOG_DEBUG);
    // esp_log_level_set(LOG_I2S_TAG, ESP_LOG_DEBUG);
    esp_log_level_set(LOG_I2C_TAG, ESP_LOG_DEBUG);
    // esp_log_level_set(LOG_SD_TAG, ESP_LOG_DEBUG);
    // esp_log_level_set(LOG_WEB_TAG, ESP_LOG_DEBUG);

    // esp_log_level_set(BT_AV_TAG, ESP_LOG_NONE);
    // esp_log_level_set(BT_APP_TAG, ESP_LOG_NONE);

    // init after restart
    led_motor_controller.set_current(restart_manager.get_led_motor());

    // fastled setup
    led_init();

    #if defined(ROBOX_FULL)
        ESP_LOGI(LOG_MAIN_TAG, "Setup mux");
        // mux.setup();
        // mux.switch_to(BleSource);
        // mux.switch_to(WebRadioSource);
        // mux.switch_to(SDSource);

        // xTaskCreatePinnedToCore(
        //     audio_task,       //Function to implement the task 
        //     "audio_task", //Name of the task
        //     6000,       //Stack size in words 
        //     NULL,       //Task input parameter 
        //     7,          //Priority of the task 
        //     &AudioCopyTask,       //Task handle.
        //     1           // Core you want to run the task on (0 or 1)
        // );

    #elif defined(ROBOX_COMPONENT_BLE)
        ESP_LOGI(LOG_MAIN_TAG, "ble start");
        ble.mux_start();

    #elif defined(ROBOX_COMPONENT_WEB)
        ESP_LOGI(LOG_MAIN_TAG, "web start");
        web.mux_start();

    #elif defined(ROBOX_COMPONENT_SD)
        ESP_LOGI(LOG_MAIN_TAG, "sd start");
        sd.mux_start();

    #elif defined(ROBOX_EXAMPLE_BLE) || defined(ROBOX_EXAMPLE_BLE_BEAT) || defined(ROBOX_EXAMPLE_SD) || defined(ROBOX_EXAMPLE_WEB) || defined(ROBOX_EXAMPLE_MULTI_WEB_FFT) || defined(ROBOX_EXAMPLE_WEB_PLAYER_BEAT) || defined(ROBOX_EXAMPLE_SD_PLAYER_BEAT)
        ESP_LOGI(LOG_MAIN_TAG, "examples start");
        player_setup();

    #endif


    #if defined(ROBOX_DEBUG_I2C) || defined(ROBOX_LCD) || defined(ROBOX_MOTOR) || defined(ROBOX_BATTERY)
    io = new RoboxIoExpander(IO_EXPANDER_W_ADDRESS);
    #endif


    #if defined(ROBOX_LCD)
        ESP_LOGI(LOG_MAIN_TAG, "lcd setup");

        screen = new RoboxLcdScreen(io);
        io->register_observer(screen, RoboxLcdScreen::io_config());
    #endif

    #if defined(ROBOX_MOTOR)
        ESP_LOGI(LOG_MAIN_TAG, "motor setup");
        motor = new RoboxMotor(io);
        io->register_observer(motor, RoboxMotor::io_config());
    #endif

    #if defined(ROBOX_BATTERY)
        ESP_LOGI(LOG_MAIN_TAG, "battery setup");
        battery = new RoboxBattery(io);
        io->register_observer(battery, RoboxBattery::io_config());
    #endif

    #if defined(ROBOX_DEBUG_I2C) || defined(ROBOX_LCD) || defined(ROBOX_MOTOR)
        ESP_LOGI(LOG_MAIN_TAG, "configure io-expander");
        io->io_configure();
    #endif

    #if defined(ROBOX_LCD)
        ESP_LOGI(LOG_MAIN_TAG, "lcd init");
        screen->init_lcd();
    #endif

    #if defined(ROBOX_BATTERY)
        battery->initBattery();
    #endif

    #if defined(ROBOX_DEBUG_CLI)
        ESP_LOGI(LOG_MAIN_TAG, "select ble source");
        debug_cli_setup();
    #endif

    #if defined(ROBOX_DEBUG_I2C)
        io->configure_outputs(0, 0x00);
        io->configure_outputs(1, 0x00);
    #endif

    #if defined(ROBOX_DEBUG_I2C_SCANNER)
        scanner_setup();
    #endif

    #if defined(ROBOX_TEST_ADC_KEY)
        adc_key_setup();
    #endif

    #if defined(ROBOX_MOTOR)
    motor->init();
    #endif


    xTaskCreatePinnedToCore(
        audio_task,       //Function to implement the task 
        "audio_task", //Name of the task
        7000,       //Stack size in words 
        NULL,       //Task input parameter 
        PRIORITY_AUDIO_TASK,          //Priority of the task 
        &AudioCopyTask,       //Task handle.
        0           // Core you want to run the task on (0 or 1)
    );

    #if defined(ROBOX_WIFI)
        wifi_setup();
    #endif

    #if defined(ROBOX_IMPROV)
        improvSerial.setDeviceInfo(
            ImprovTypes::ChipFamily::CF_ESP32,  // chipFamily
            "Robox-2024",                       // firmware name
            "0.0.1",                            // firmware version
            "Robox 2024"                        // device name
        );
    #endif

    restart_manager.setupWifi();

}

void loop() {
    #if defined(ROBOX_TEST_ADC)

    if (millis() > adc_timekeeper) {
        // esp_err_t r = adc2_get_raw(ADC2_CHANNEL_4, ADC_WIDTH_BIT_12, &adc2_pin13);
        // Serial.printf("adc2 pin13[%s]: %d\n", (r == ESP_OK) ? "ADC OK" : "FAIL", adc2_pin13);
        // adc1_config_width(ADC_WIDTH_BIT_12);
        // adc2_pin13 = adc1_get_raw(ADC1_CHANNEL_3);//, ADC_WIDTH_BIT_12, &adc2_pin13);
        // Serial.printf("adc1 pin39[]: %d\n", adc2_pin13);

        // Serial.printf("adc1 pin 39: %ld\n", analogReadMilliVolts(39));
        // Serial.printf("mux last %ld\n", beat_loop_timestamp);

        if (beat_loop_timestamp_previous == beat_loop_timestamp) {
            // Serial.println("no audio playing");

            motor->shutdown_idempotent();
        } 
        else {
            if (led_motor_controller.is_motor_enabled()) {
                motor->enable_idempotent();
            }
            // Serial.println("audio playing");
        }

        beat_loop_timestamp_previous = beat_loop_timestamp;
        adc_timekeeper = millis() + 500;
    }
    #endif


    #if defined(ROBOX_FULL)
        // mux.copy();
    
    #elif defined(ROBOX_EXAMPLE_BLE) || defined(ROBOX_EXAMPLE_BLE_BEAT) || defined(ROBOX_EXAMPLE_SD) || defined(ROBOX_EXAMPLE_WEB) || defined(ROBOX_EXAMPLE_MULTI_WEB_FFT) || defined(ROBOX_EXAMPLE_WEB_PLAYER_BEAT) || defined(ROBOX_EXAMPLE_SD_PLAYER_BEAT)
        player_loop();

    #elif defined(ROBOX_COMPONENT_BLE)
        ble.mux_copy();

    #elif defined(ROBOX_COMPONENT_WEB)
        web.mux_copy();

    #elif defined(ROBOX_COMPONENT_SD)
        sd.mux_copy();

    #endif


    // #if defined(ROBOX_LCD)
    //     // ESP_LOGI(LOG_MAIN_TAG, "LCD loop");

    //     // screen->lcd_gfx_test();
    //     screen->lcd_menu_loop();
    // #endif

    #if defined(ROBOX_DEBUG_CLI)
        debug_cli_loop();
    #endif

    // #if defined(ROBOX_MOTOR) || defined(ROBOX_BATTERY)
    //     // check interrupt
    //     io->loop();
    // #endif

    #if defined(ROBOX_DEBUG_I2C)
        ESP_LOGI(LOG_MAIN_TAG, "IO expander write");
        io->set_output(0, 0x00);
        // io->set_output(1, 0x00);
        delay(100);
        io->set_output(0, 0x80);
        // io->set_output(1, 0xFF);
        delay(100);

        // ESP_LOGI(LOG_MAIN_TAG, "IO expander read");
        // uint8_t data = io->get_configure_outputs(1);
        // ESP_LOGI(LOG_MAIN_TAG, "IO expander read %2x", data);

    #endif

    // #if defined(ROBOX_DEBUG_I2C_SCANNER)
    //     scanner_loop();
    //     delay(10000);
    // #endif

    // #if defined(ROBOX_MOTOR)
    // if (timekeeper < millis()) {
    //     Serial.printf("new motor program. timekeeper: %ld, program %d\n", timekeeper, (motor_test_program % MOTOR_TEST_PROGRAMS));
    //     timekeeper += 5000;


    //     switch (motor_test_program % MOTOR_TEST_PROGRAMS)
    //     {
    //     case 0:
    //         motor->set_direction(0, 0);
    //         motor->set_speed(0.3, 0.3);
    //         break;

    //     case 1:
    //         motor->set_direction(1, 1);
    //         motor->set_speed(0.3, 0.3);
    //         break;
        
    //     case 2:
    //         motor->set_direction(1, 0);
    //         motor->set_speed(0.3, 0.3);
    //         break;

    //     case 3:
    //         motor->set_direction(0, 1);
    //         motor->set_speed(0.3, 0.3);
    //         break;

    //     // case 4:
    //     //     motor->set_direction(0, 1);
    //     //     motor->set_speed(0.3, 0.3);
    //     //     break;

    //     default:
    //         break;
    //     }

    //     motor_test_program++;
    // }
    // #endif

    // #if defined(ROBOX_IMPROV)
    //     improvSerial.handleSerial();
    // #endif

    // led_breath(true, r_blue);

    // #if defined(ROBOX_WIFI_MANAGER)
    // doWiFiManager();
    // #endif
    if (mux.get_current_source() == BleSource) {
        if (is_ble_on == false) {
            led_breath(true, r_blue);
        }
        else if ((is_ble_on = true) && (is_ble_connected == false)) {
            led_breath(false, r_blue);
        }
    }
    
}

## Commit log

2024-02-19 make a wrapper for the SED1530 driver so that the updateWholeScreen runs in a task.
2024-02-19 small refactor pin definitions
2024-04-17 Post ESP32 selection crisis - continuing with ESP32-MINI-1 dual core - adding pinout docs - adding examples for BLE-A2DP, ICE-cast webstream, uSD mp3 files (mux interface might be currently broken)
    [ESP32_4MB_OTA_NOSPIFS.csv, ESP32_8MB_OTA_SPIFS.csv, ESP32_OTA_8M.csv]
2024-05-02 adding I2C driver and integration with LCD driver
2024-05-03 cleanup I2C and LCD driver
2024-05-16 add initial motor driver code
2024-05-23 debug I2C, adapt LCD code to class, extract I2C into seperate class, create stubs for motor and battery classes
2024-07-09 change flash laout to 1 app partition
    [ESP32_4MB_1APP.csv, ESP32_8MB_OTA_SPIFS.csv, ESP32_OTA_8M.csv]
2024-07-11 integrate adc keys
2024-07-11 example buttons switch audio source
2024-07-11 add long press feature to buttons
2024-07-11 change GEM button type
2024-07-13 initial threaded GUI task (GEM)
2024-07-24 normal / selected button icon sets & button presses handled in custom draw loop
2024-07-25 audio play menu: make buttons selectable, add switch and settings submenus
2024-07-25 workaround switching to submenus
2024-07-27 add functionality to gui buttons + add led&motor gui button
2024-07-27 fix header signature, add millis timer to button press events
2024-07-28 switch volume and next/previous buttons
2024-07-29 initial battery voltage task
2024-07-29 fix motor direction
2024-07-31 Re-enable buttons
2024-07-31 Increase i2c speed so redraws go faster
2024-08-01 update motor speed and move wifiManager to end of setup
2024-08-03 add instructions for fixed flash voltage
2024-08-03 feature: led effects in other components
2024-08-03 fix for I2C read
2024-08-03 update test motor speed
2024-08-03 add restart manager for audio switch https://github.com/pschatzmann/arduino-audio-tools/discussions/26#discussioncomment-1561091
2024-08-04 remove led_breath test
2024-08-04 switch to htmx
2024-08-06 add led motor control (for gui)
2024-08-06 added battery reading and motor disabling. still an issue with boot-loop/issues after selecting source (not when usb is plugged in it seams)
    [main.cpp]
2024-08-08 reboot manager: keep led motor controller state
    [main.cpp]
2024-08-09 integrate battery
2024-08-09 battery integration 2
2024-08-10 animatie hot button
2024-08-10 initial groundwork wifi credetnials reset
2024-08-10 add ip address and battery voltage labels to RO menu
2024-08-10 battery charging marker feature
2024-08-11 ble marker feature + led breathing effect when connection + fix issue ble remote volume update not updating the screen)
    [main.cpp]
2024-08-11 test esp web tools software update button
2024-08-11 fix source switch crash
2024-08-11 I2C scanner image
2024-08-11 fix order of charging marker decision loop
2024-08-16 fix charging maker
2024-08-23 Added laser cut files, 3D-print files, pcb-design files
    [1-full-set.3mf, AUDIO.SchDoc, Bill of Materials-JSP016RB(JSP016RB_NO_TH_COMP).xls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]
2024-08-28 Update Readme.md
    wat extra basic info toegevoegd om deelnemers op de hoogte te stellen.
2024-10-22 make motor speed and led brightness configurable
2024-10-30 updated wheel axle holder
    [1-full-set.3mf, fully-printed-wheel.3mf]
2024-12-06 small fixes: settings enum select order, battery charging full workaround.
